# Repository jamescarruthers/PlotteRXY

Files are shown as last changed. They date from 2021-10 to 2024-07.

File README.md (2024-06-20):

# PlotteRXY
A machine designed to be your second plotter after an AxiDraw or vintage plotter.

# Why?
I really enjoyed the flexibility of my AxiDraw, and the speed of my Roland DPX-2200. I wanted something of a halfway house, with the pen flexibility of the AxiDraw and the speed and size of the Roland.

I set myself a few design requirements; enclosed inside a frame, scalable to any size including "massive" and a solenoid for fast pen lift.

I chose CoreXY pretty much just because I thought it was cool. It probably limits the scalability a bit as I expect belt droop might be an issue for _really_ huge plotters.

It uses an off-the-shelf FYSETC E4 controller board, which also has the benefit of being wifi enabled and has a web GUI built in.

The toolchain is fairly simple; SVG ingested in to VPYPE and it's G-code plugin. The G-code is uploaded through the web browser.

# How?

The build is fairly simple, you'll need access to a 3D printer to print off the various parts. Most of the parts are symetrical, so it's a fairly simple list of parts.

Ideally, print the parts in at least PETG but ASA or ABS would probably be better. My prototype machine has had no issues with matte PLA, which is probably the most brittle filament there is.

Suggested print settings; 4 walls, 5 top and bottom layers, 40% cubic infill.

Print time on a Bambu P1S is approx 13 hours at normal speed, and can be done over two plates. It uses 350g of filament in total.

The rest of the parts you'll need are here; https://docs.google.com/spreadsheets/d/1bjWigQsAcE3DGmHS4qicfL3H79G1RvEPnRx3VYNnScU/

There is a build guide in the hardware folder.

The firmware folder contains the machine configuration for use with FluidNC.

The software folder contains a configuration file for use with vpype and vpype-gcode.

# Donate

If you appreciate this project, please consider donating; https://www.paypal.com/donate/?hosted_button_id=BHS97LUK2LCB6

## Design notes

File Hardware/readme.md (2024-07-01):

*The 2040 Y-axis is depreciated at this time.* Only print one Y-axis folder - depending on what extrusion profile you are using for your y-axis. Unless you are making a giant A0 or larger plotter then use the 2020 sized version. Note that this design hasn't been tested above A1 size.

# How long should my extrusions be?

Let's say you want to build an A2 machine; 600 x 420 (rounded up)

X extrusion = width + 260 = 600 + 260 = 860mm

Y extrusion = length + 200 = 420 + 200 = 620mm

Y axis = Y extrusion - 13 = 607mm

These numbers have a bit of excess to allow a bit of movement around the outside of the plot area.

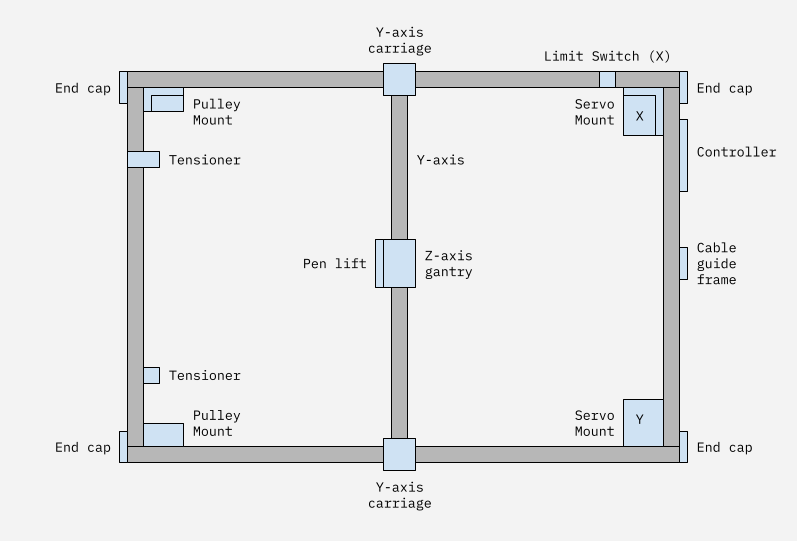
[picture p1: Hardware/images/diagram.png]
Naming diagram


# Hardware build guide

1. Print out a corner pulley mount and check that it fits snuggly into your v-slot extrusion. If it doesn't you might need to recalibrate your printer.
2. Print out all the parts. The number at the end of the filename is the quantity you'll need — so Pulley_2.3mf means you need 2.
3. Layout out the extrusion and printed parts on a table according to the diagram above, work out where you will need to insert t-nuts. This is important because once you start assembly certain t-nuts are impossible to insert without loosening and/or disassembling.
4. Build up the z-axis gantry and slide it on to the y-axis. The wheels should have shims and spacers on either side.
5. Build up the y-axis carriages and attach them to the y-axis extrusion. All pulleys sit on a single shim and have two shims between the F605 bearings. Keep the screws that hold it to the y-axis loose for now.
6. Install the end caps and servo mounts to the extusions so you have an open sided C shape. Note the orientation of the servo mounts, they are opposite ways up with the flat part in the middle of the extrusion.
7. Slide the whole y-axis assembly on to the extrusion.
8. Install the pulley mounts, end caps and attach the final extrusion to close the frame.
9. Adjust all the mount screws until the frame is square. Adjust the eccentric nuts. The y-axis should slide left to right freely. Tighten the screws that hold the y-axis in place.
10. Install all the pulleys. They pulleys should sit on a single shim spacer, with two shims in between the two bearings.
11. Install the servos in to the servo mounts, being sure to vertically align the toothed pulley with the pulleys on the mount. Depending on the pulley you may need to use one of the stepper spacers between the motor and the mount to align the belt so that it sits in the middle of the teeth on the pulley.
12. Install belts and attach to the belt tension plate. They should not be tight at this stage — but should not droop. Leave at least 80mm of extra belt so that you can adjust it later.

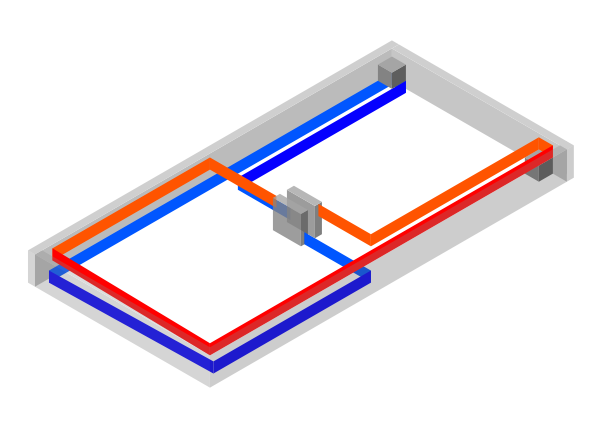
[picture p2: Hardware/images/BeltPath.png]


13. Use the tensioners to get the belt tight. It should not be super tight, but the belt should not droop.
14. Attach the belt tension plate to the z-axis gantry.
15. Move the y-axis towards and up against the corner pulley mounts. Check that the y-axis is square by ensuring the gap between the rounded part of the y-axis carriages have equal space against the corner pulley mounts. Each y-axis carriage should sit flat against the corner pulleys. If they're not, then this means each belt has uneven tension. Use the belt tensioners to adjust, they should only need minimal movement.
16. Build up pen lift and install on to gantry.

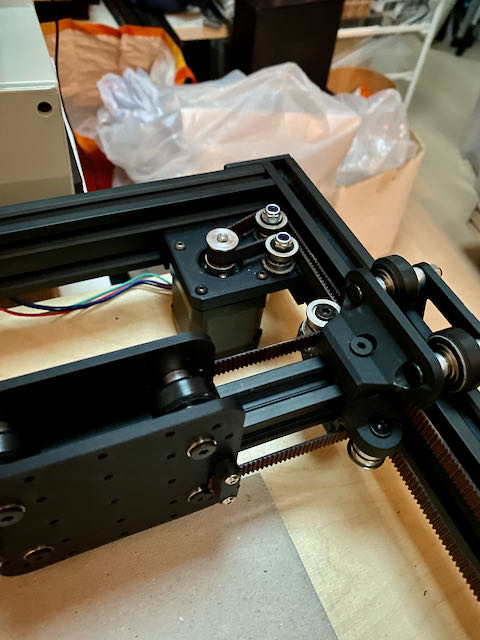
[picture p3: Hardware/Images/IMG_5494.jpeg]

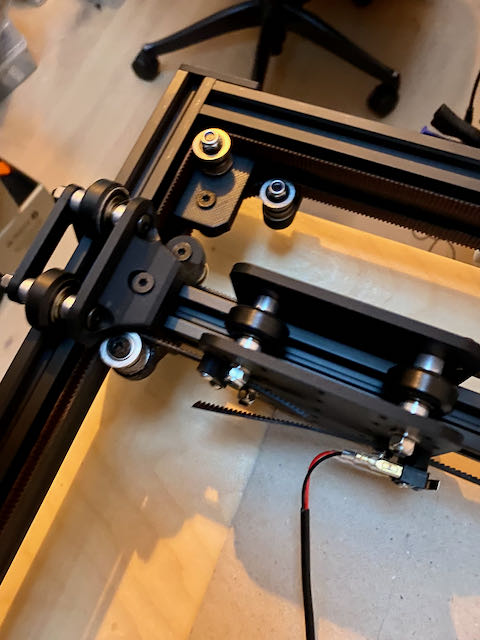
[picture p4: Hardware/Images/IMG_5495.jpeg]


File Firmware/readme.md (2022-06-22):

PlotterXY uses FluidNC: https://github.com/bdring/FluidNC

1. Install FluidNC on your FYSETC E4.
2. Upload the yaml config file to your board.
3. Restart the machine.

Be sure to use the supplied heatsinks, they should go on the rear of the board. I recommend using up the two spare heatsinks on the front of the ICs too.

*Note that the Y stepper is connected to the connector labelled Z-MOT – this is just to help thermals.

Connections:
* X-MOT: X stepper motor
* Z-MOT: Y stepper motor
* X-MIN: X limit switch
* Y-MIN: Y limit switch (on the z-axis gantry)
* HEATER: Solenoid

Check that these two jumpers are set for UART:

Jumpers

Before switching on the first time, move the gantry in to the centre of the work area. Turn on and connect to the web UI. Click on the clear alarm button. Use the jog function to check that the gantry moves in the correct direction. If it does not, then adjust the direction_pin in the config file from high to low on the relevant axis.

You will need to adjust the max_travel_mm and mpos_mm values in the config file for both the x and y axes to reflect the size of your plotter. The mpos_mm value should match the max_travel_mm. It is best to home the machine with the default settings, and then use a tape measure to get the dimensions. When homing move the z-gantry somewhere close to the top right by hand before you turn the plotter on, a couple of centimetres away from the limit swiches. Start off configuring it with a smaller size and then check out the movement of the machine with the jog function to make sure that the z-axis doesn't crash in to the right and bottom extrusions when you move it to 0,0.

Depending on your pen lift mechanism and pen weight you may need to adjust the solenoid pull_percent and hold_percent if the solenoid does not manage to lift or hold the pen.

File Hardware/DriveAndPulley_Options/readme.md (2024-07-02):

There are a few different options for drive and pulley configurations depending on what you want to achieve.

V2 is suggested for new builds as it's a much neater layout, allowing one end of the plotter to be free of belt and any kind of wiring. It also drives the middle of the belt, rather than more towards one end.

Note that there is no "upgrade path" from V2 to 4WD. If you want 4WD use the V1 mounts. There's nothing wrong with V1, it just drove the "wrong" part of the belt - which happens to be the right part for 4WD. If you _really_ want to go 4WD with V2 then you could use the V1 stepper mounts, but it's not optimal.

## V1 Original

* 2 x V1 stepper mount
* 2 x V1 pulley mount

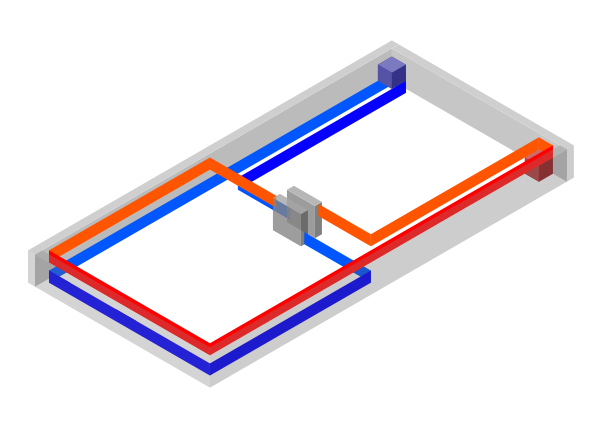
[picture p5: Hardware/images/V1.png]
V1


## V1 with 4-wheel-drive

* 2 x V1 stepper mount
* 2 x V1 stepper mount AWD

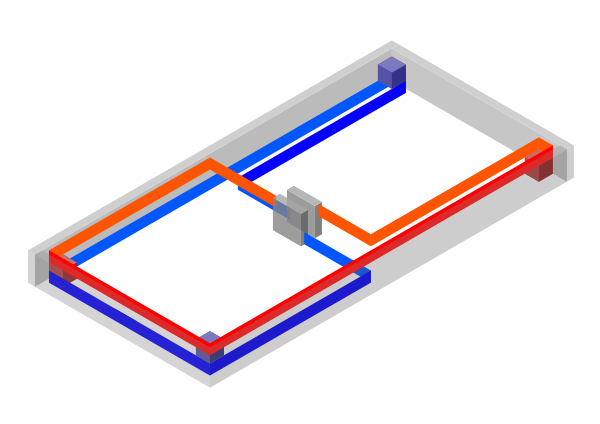
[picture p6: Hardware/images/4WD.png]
V1AWD


## > Note: V2 is currently untested - use at your own risk

## V2

* 2 x V2 stepper mount
* 2 x V2 pulley mount

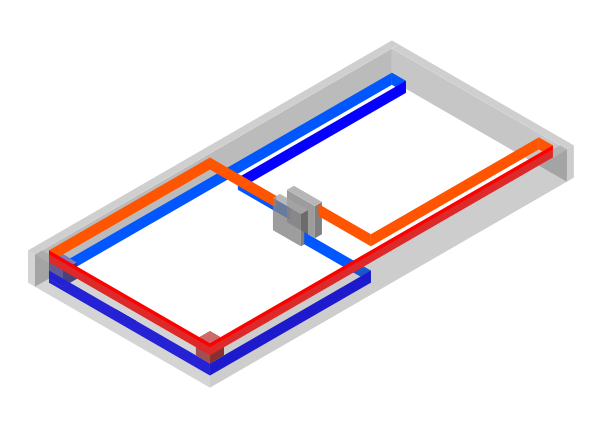
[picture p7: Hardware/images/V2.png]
V2


## V2 with central drive

* 1 x central drive
* 2 x V1 pulley mount
* 2 x V2 pulley mount

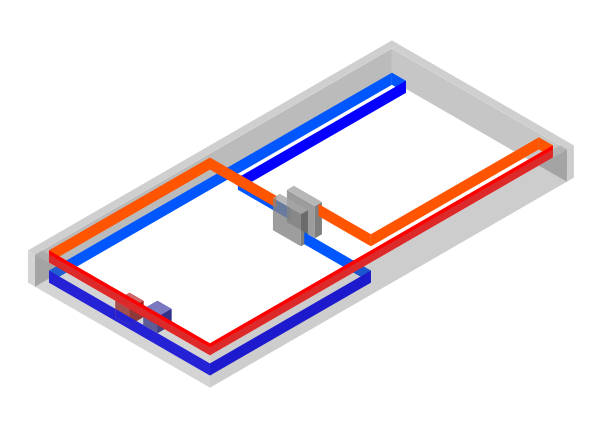
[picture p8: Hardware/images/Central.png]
V2 central drive


This configuration mounts the two steppers together.

## 4-wheel-drive tensioning procedure

Use the following procedure to make sure the pulley teeth are synchronised.

1. Power off the plotter.
2. Disconnect the two 4WD steppers from the controller board and loosen the two grub screws on both the 4WD pulleys.
3. Adjust the tension on both belts.
4. Power the plotter on.
5. Ensure the 4WD pulleys are engaged with the belt.
6. Tighten the grub screws on the 4WD pulleys, ensuring that they are not tightened against the flat of the D shaft. The pulley should not move as you tighten the grub screws.
7. Power the plotter off.
8. Reconnect the 4WD steppers.
9. Power the plotter on.

## Thoughts on drive position

Our aim is to drive a belt somewhere in the middle so that we have equal lengths on either side. A long belt is going to be more prone to vibration.

Below is a diagram showing the middle of the belt at different extents.

The red line shows the range and the red arrow shows the middle of the range. This is the ideal position for the driven pulley. We are constrained by putting the motor in a corner - luckily, a corner is not far away.

For 4-wheel-drive we would want to position motors at either end of the range.

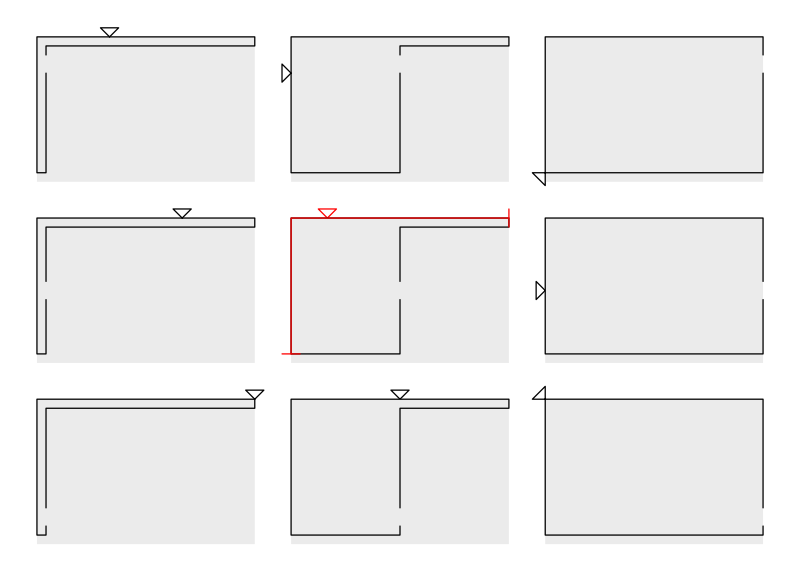
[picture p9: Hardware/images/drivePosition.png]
V2 central drive


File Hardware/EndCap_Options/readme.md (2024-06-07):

## End Cap Options

For a standard build you want to use the 4 x plain end caps.

For a 4WD build where you have motors at either end then choose either hole or XH. Depending on how you want to route your wires, you might want to use a mix of the plain and the end cap with XH or holes.

The XH variant has a slot that you can push an XH connector through - the most common type of connector on a stepper motor.

The hole variant is just a plain 4mm hole that you can put cables through.

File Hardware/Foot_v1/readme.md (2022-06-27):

These are some basic feet to get started with.

The lower part should be a tight enough fit with the foot so that it does not move.

The lower part needs to be secured to your worksurface with double sided tape.

An alternative would be to attach some rubber sheet to the lower part with double sided tape.

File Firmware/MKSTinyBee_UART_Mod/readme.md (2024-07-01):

To modify the MKS TinyBee to work with UART you'll need to jump various points on the board.

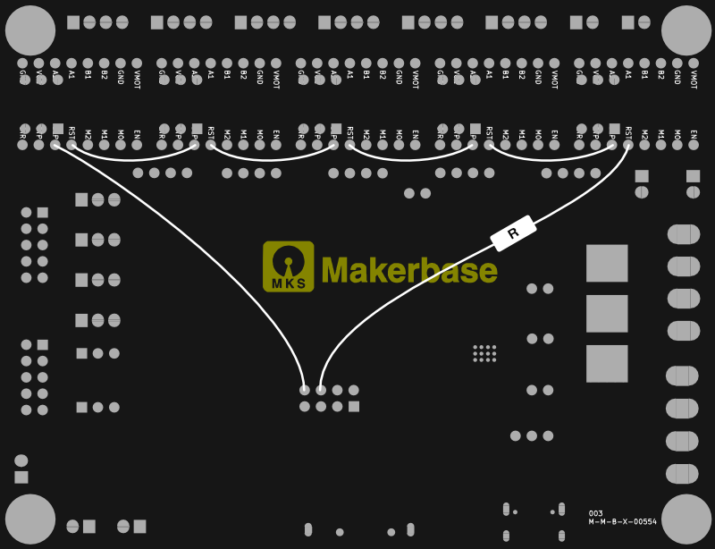
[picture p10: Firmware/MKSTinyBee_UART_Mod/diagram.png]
Diagram of modification


The resistor I used was 330R - you may need to try higher or lower.

Before installing the drivers switch all the dip switches to low.

Set the address of the X, Y and Z:

X = off off off
Y = on off off
Z = off on off

E0 is the secondary X - so set this to the same as X.
E1 is the secondary Y - so set this to the same as Y.

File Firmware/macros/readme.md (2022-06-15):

A series of macros useful for operating the plotter.
The park macro will need to be updated to reflect the size of your machine.

zero = move to 0,0

park = move the gantry out of the way to the top right

The A*_UR macros are for helping to align materials. Run the home macro, then place the bottom left corner of your material where the pen is – then run the A*_UR macro and align the top right corner.

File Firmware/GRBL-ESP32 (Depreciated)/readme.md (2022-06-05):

PlotterXY uses Grbl_ESP32: https://github.com/bdring/Grbl_Esp32

1. Download Grbl_ESP32. Follow the instructions.
2. Copy the PlotterXY_E4.h file to the machines folder and adjust the config.h to point towards it. See the section "Customize "Grbl_Esp32/src/Machine.h"" in the installation part of the wiki.
3. Compile and upload to the FYSETC E4 board. (remember that the board needs power!)

Connections:
* X-MOT: X stepper motor
* Y-MOT: Y stepper motor
* X-MIN: X limit switch
* Y-MIN: Y limit switch (on the z-axis gantry)
* HEATER: Solenoid

You will also need to use two jumpers to enable TMC2209 UART:

Jumpers

You will need to adjust the DEFAULT_X_MAX_TRAVEL and DEFAULT_Y_MAX_TRAVEL to reflect the size of your plotter. It's safer to do this after the firmware is compiled and uploaded, and you can use the jog function to move the gantry in to the 0,0 position.

Before switching on the first time, move the gantry in to the centre of the work area. Turn on and connect to the web UI. Click on the clear alarm button. Use the jog function to check that the gantry moves in the right direction. If it doesn't, then adjust the stepper motor direction in config.

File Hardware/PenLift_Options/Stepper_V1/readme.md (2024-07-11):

# Stepper pen lift

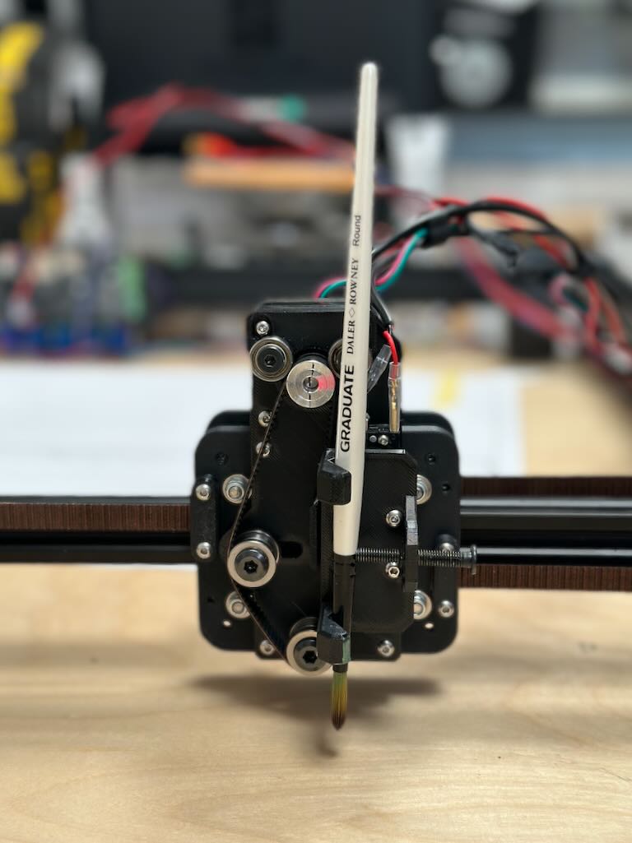
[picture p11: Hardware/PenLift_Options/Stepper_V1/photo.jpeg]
Stepper pen lift


This pen lift allows gravity and driven functions by adjusting a pulley.

Additional components required:

* Nema 17 stepper motor - pick the slimmest and lightest you can find
* 20t pulley - same used on the belt drive steppers
* 4 x 605Z bearings - same as used on all other pulleys
* 9mm 2GT belt - same as used for the drive belts
* 2 x 3mm spacers or 6 x 1mm spacers - same as used on all other pulleys
* 2 x 16mm M5 for pulleys
* 1 x 5mm t-nut - same as used for securing everything else to aluminium rail
* 1 x LWL7B 55mm guide rail - same as the solenoid lift
* 1 x limit switch and associated wiring - same as used on the limit switches for the X and Y axis
* 1 x M5 bolt for pen holder
* 2 x 605 bearings for the pulley keeper - this is the same as the rest of the plotter BUT without the flange
* Various M2 and M3 screws to mount the arm, penholder, limit switch and stepper motor

The pulley keeper should not be tight, it should just sit on the belt.

The belt should be installed with the adjustment pulley to the left, move the pulley to the right to loosen and enable "drop" mode.

The screw tip is a very basic item to put on the end of the pen holder bolt - it's a clumsy solution at the moment.

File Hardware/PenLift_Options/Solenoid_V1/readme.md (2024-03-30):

You will also need a suitable size e-clip, as well as a very short piece of silicon tubing to create a bumper.

The bumper should be just long enough to stop the solenoid from clacking.

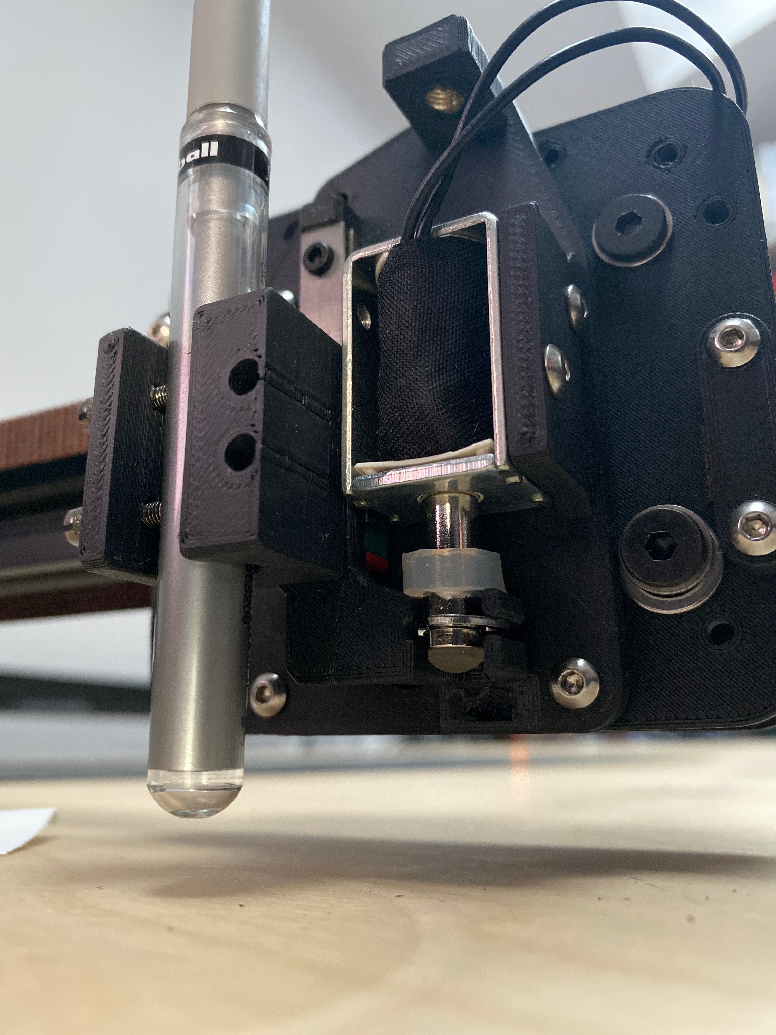
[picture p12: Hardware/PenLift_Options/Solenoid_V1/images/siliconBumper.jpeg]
Naming diagram


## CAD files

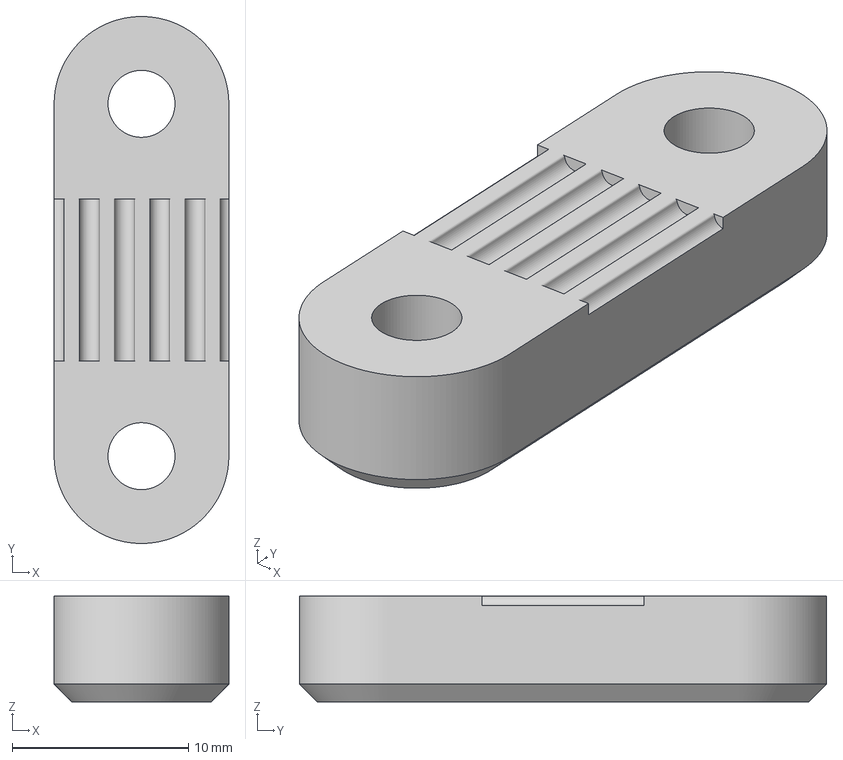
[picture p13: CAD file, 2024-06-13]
Hardware/BeltClamp_3.3mf
9.92 x 29.9 x 6.00 mm

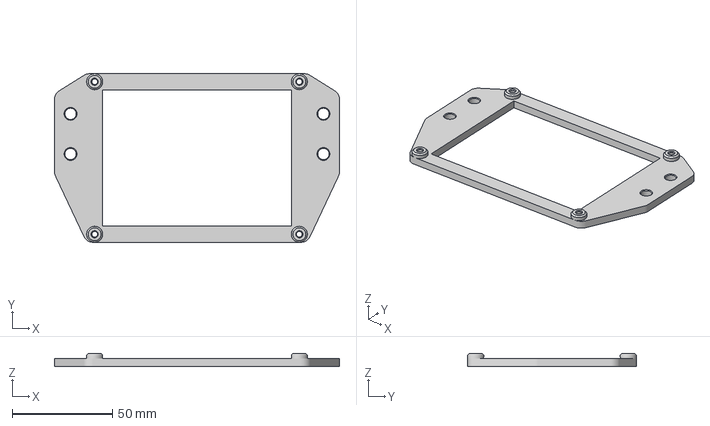
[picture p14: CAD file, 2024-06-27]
Hardware/BoardMount_Options/MKSTinyBee_Mount.3mf
142.0 x 84.0 x 6.60 mm

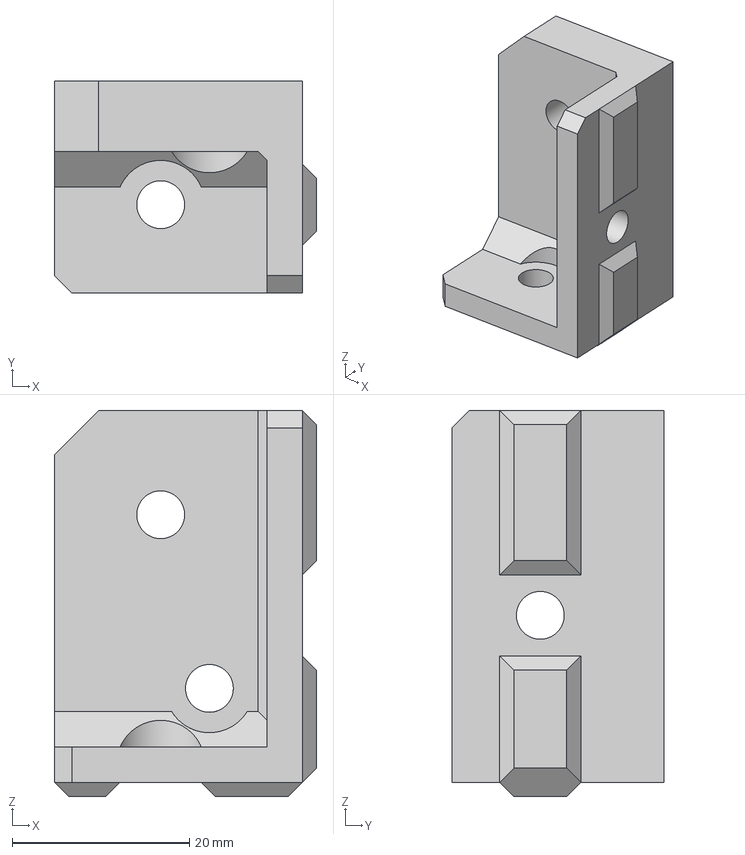
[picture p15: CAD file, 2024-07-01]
Hardware/DriveAndPulley_Options/V2_PulleyMount_2.3mf
29.6 x 24.0 x 43.6 mm

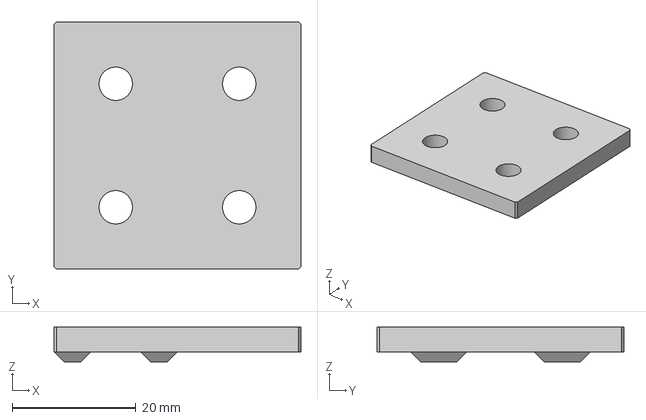
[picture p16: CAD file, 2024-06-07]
Hardware/EndCap_Options/EndCap.3mf
40.0 x 40.0 x 5.60 mm

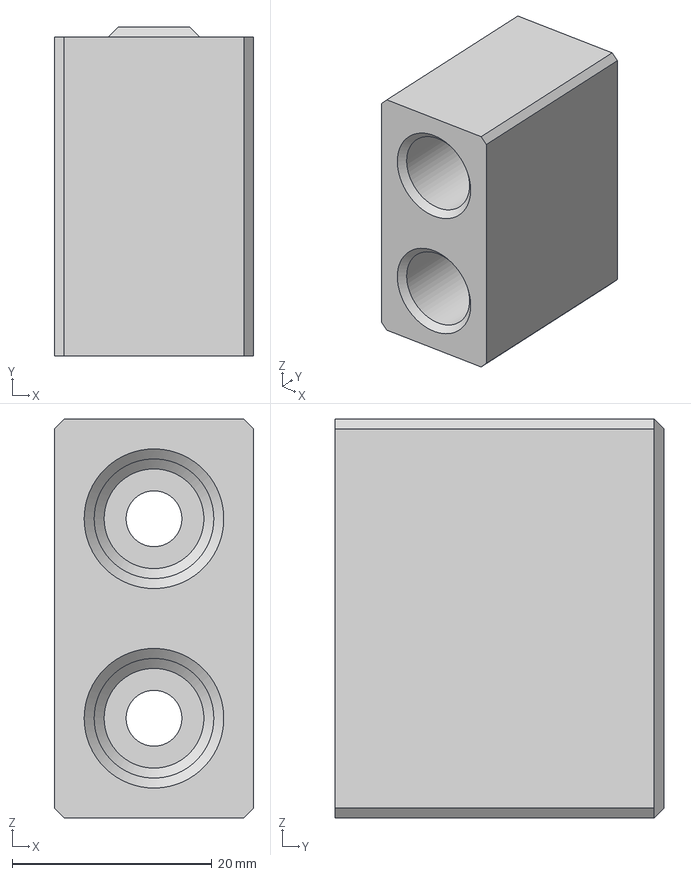
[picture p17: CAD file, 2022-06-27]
Hardware/Foot_v1/Foot_4.3mf
20.0 x 33.0 x 40.0 mm

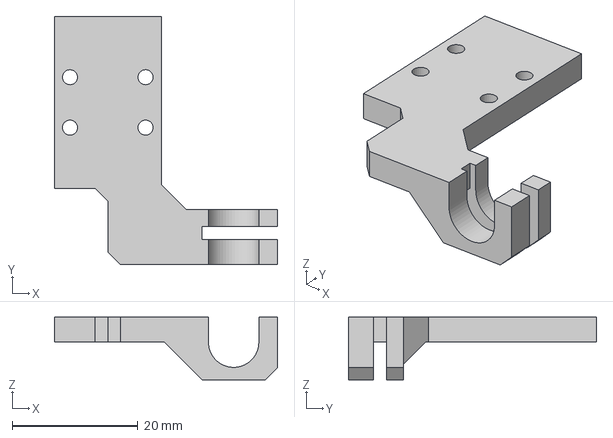
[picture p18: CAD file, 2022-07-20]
Hardware/PenLift_Options/Solenoid_V1/Lever.3mf
35.5 x 39.4 x 10.0 mm

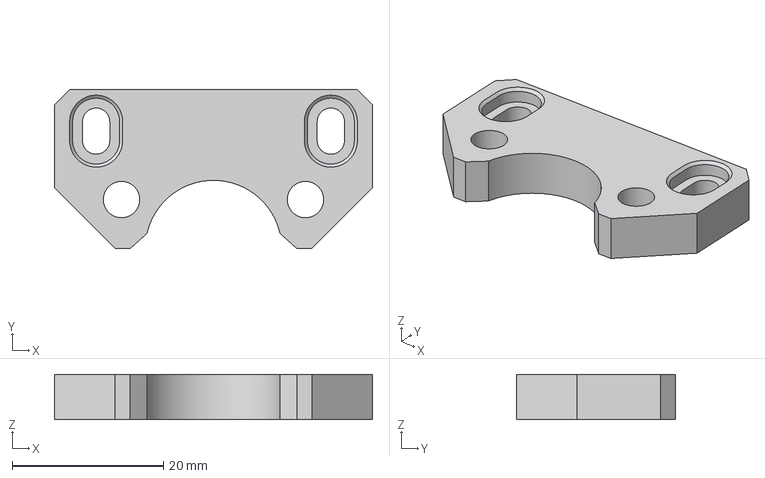
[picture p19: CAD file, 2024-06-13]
Hardware/PenLift_Options/Stepper_V1/pulleykeeper_1.3mf
42.0 x 21.0 x 6.00 mm

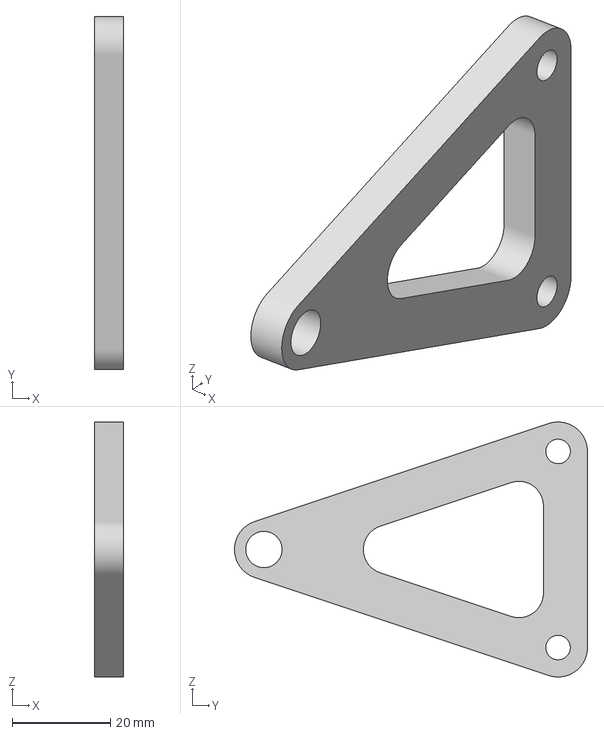
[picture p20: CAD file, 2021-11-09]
Hardware/Y-axis_Options/Y-axis_2020/YAxisCarriageSupport_2.3mf
6.00 x 72.0 x 52.0 mm

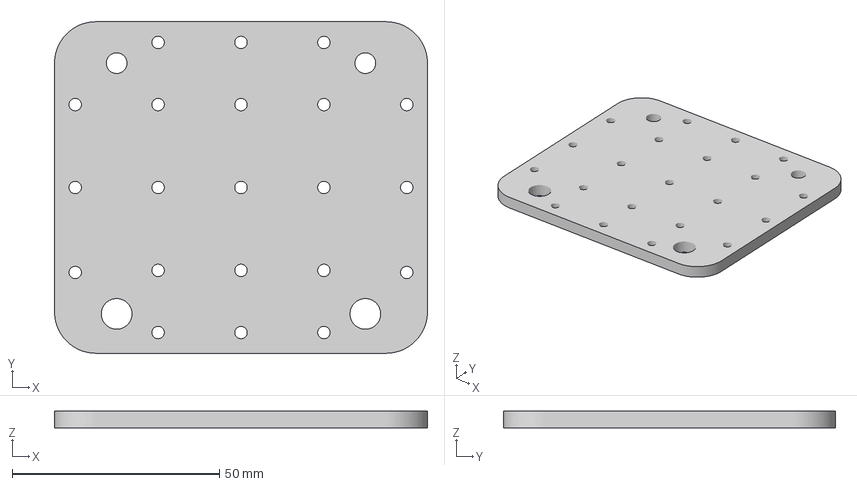
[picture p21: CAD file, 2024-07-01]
Hardware/Y-axis_Options/Y-axis_2040/ZAxisGantry2040_2.3mf
90.0 x 80.0 x 4.00 mm

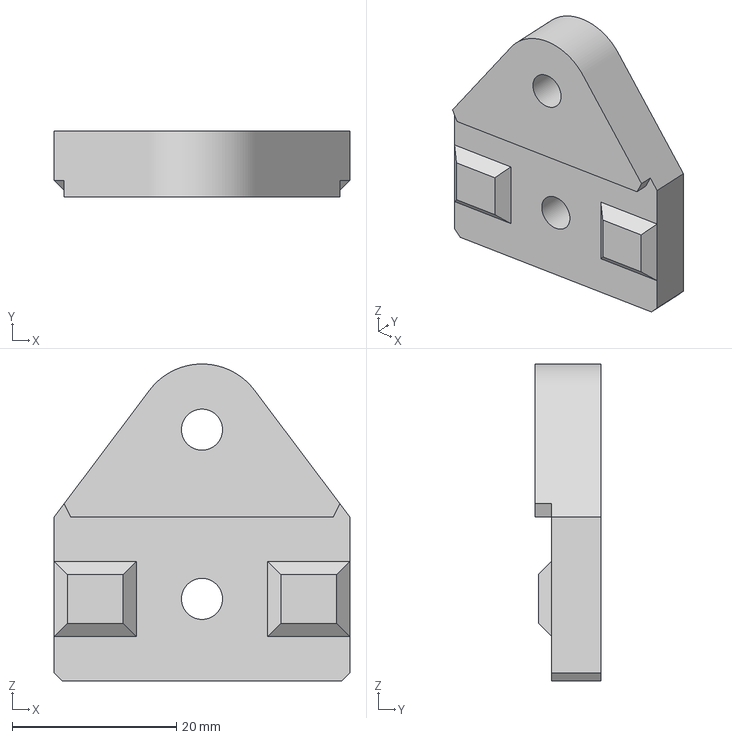
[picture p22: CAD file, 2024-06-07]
Hardware/BeltTensioner_2.3mf
36.0 x 8.00 x 38.6 mm

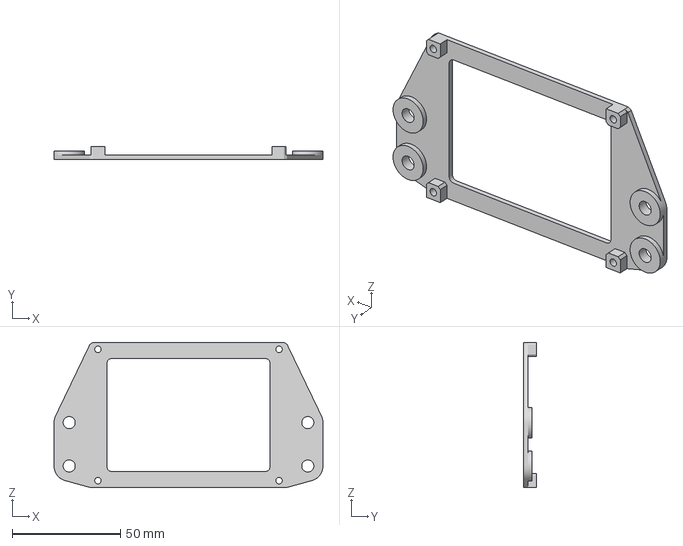
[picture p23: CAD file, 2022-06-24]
Hardware/BoardMount_Options/FYSETC_E4_Mount.3mf
124.0 x 6.00 x 67.0 mm

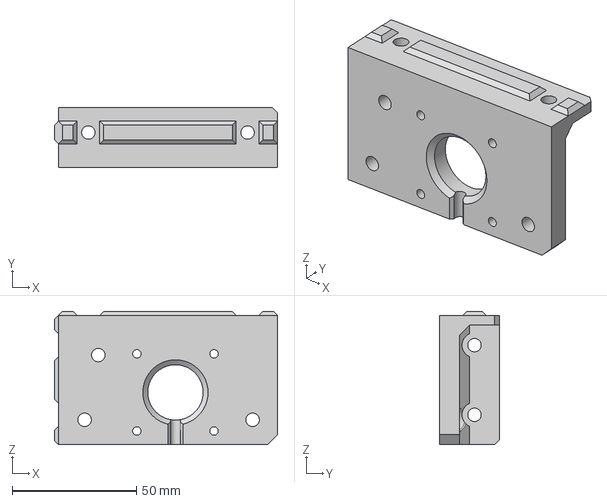
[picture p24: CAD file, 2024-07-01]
Hardware/DriveAndPulley_Options/V2_StepperMount_2.3mf
89.6 x 24.0 x 53.6 mm

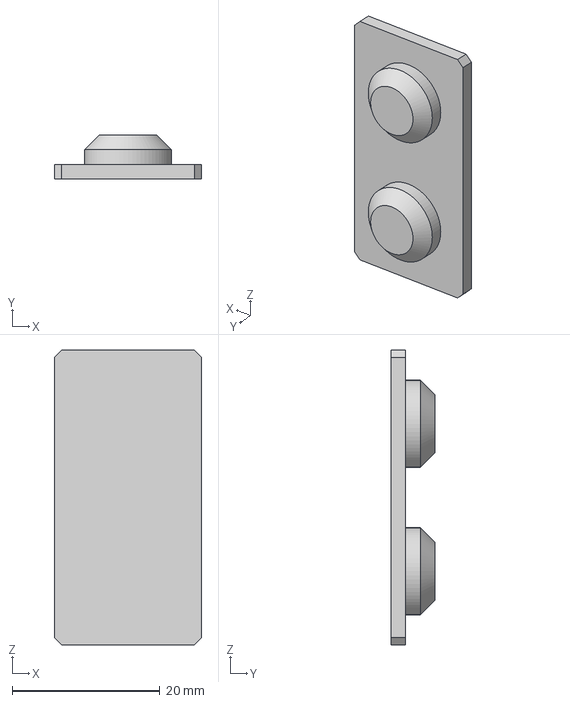
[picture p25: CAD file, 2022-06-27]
Hardware/Foot_v1/FootLower_4.3mf
20.0 x 6.00 x 40.0 mm

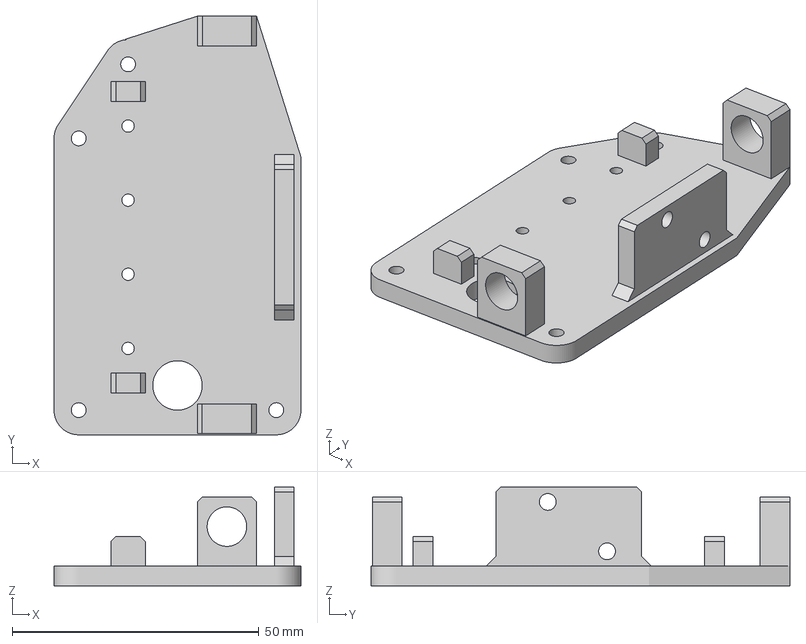
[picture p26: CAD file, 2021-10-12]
Hardware/PenLift_Options/Solenoid_V1/Mount.3mf
50.0 x 84.8 x 20.0 mm

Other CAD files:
Hardware/EndCap_Options/EndCap_Hole.3mf
Hardware/PenLift_Options/Stepper_V1/penholder_1.3mf
Hardware/Y-axis_Options/Y-axis_2020/ZAxisGantry_2.3mf
Hardware/Y-axis_Options/Y-axis_2040/YAxisCarriageSupport_2.3mf
Hardware/BeltClampLimit_1.3mf
Hardware/BeltTensionPlate_1.3mf
Hardware/CableClip_6.stl
Hardware/CableGuide_Frame.3mf
Hardware/CableGuide_Gantry.3mf
Hardware/DriveAndPulley_Options/CentralDrive_1.3mf
Hardware/DriveAndPulley_Options/StepperSpacer_2.3mf
Hardware/DriveAndPulley_Options/V1_PulleyMount_2.3mf
Hardware/DriveAndPulley_Options/V1_PulleyMount_Cover_A_1.3mf
Hardware/DriveAndPulley_Options/V1_PulleyMount_Cover_B_1.3mf
Hardware/DriveAndPulley_Options/V1_StepperMount_2.3mf
Hardware/DriveAndPulley_Options/V1_StepperMount_4WD_2.3mf
Hardware/DriveAndPulley_Options/V1_StepperMount_Cover_A_1.3mf
Hardware/DriveAndPulley_Options/V1_StepperMount_Cover_B_1.3mf
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

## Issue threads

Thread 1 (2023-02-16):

STEP Files Available?

ScottEgan, 2023-02-16:
Hi,

Awesome project, thanks for all the detail!

I'm in the process of modifying my plotter to be corexy and would like to use some of your parts with slight modifications. Do you have the STEP files available?

Thank you!

jamescarruthers, 2023-02-23:
Hi,

The project is designed in Fusion 360 — so I don't think STEP is available.

James

ScottEgan, 2023-02-23:
Hi James,

Thank you for the reply. Is it possible to export the native Fusion files then? I should be able to handle converting them.

TacyPW, 2024-03-15:
it would be really nice to have the fusion files in the repo as well

lambda1103, 2024-06-17:
Just to second (or third :D) this, I'd also appreciate it if you could share the .f3d file. Would be very helpful for assembly and small modifications.

theredwonder, 2024-09-03:
Wanted to also add an upvote for native CAD files. A ZIP of the Fusion360 assembly would be huge! All of the parts in STEP format would also be super helpful.
https://www.reddit.com/r/Fusion360/comments/1691l3g/export_formats_fusion_360_personalfree/

Looking to start a build on this soon, but am starting with a slightly different aluminum extrusion. Would love to tweak to fit. Thanks!

mattkerrison, 2025-03-03:
@jamescarruthers any chance of an update here? Either the f3d file or step files? I have a heap of Vslot left over from a cnc build but a lot of it isn’t 2020 or 2040 so it’d be good to adapt the 3d printed parts

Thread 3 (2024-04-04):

BOM Eccentric spacer count

TacyPW, 2024-04-04:
The BOM only lists 4 Ecc. Spacers for the Y axis gantries but as far as i can tell 4 more are needed for the Z gantry as well.

jamescarruthers, 2024-04-04:
Good catch! Thank you! Have updated the BOM.

Closed 2024-04-04.

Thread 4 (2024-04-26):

FluidNC Config File not compatible with latest version of fluidnc

TacyPW, 2024-04-26:
The way that fluidnc wants uart channels to be set up has changed, see [this page](http://wiki.fluidnc.com/en/config/uart_sections) of the wiki.

> Trinamic UART devices like TMC2208 and TMC2209 no longer support the subordinate "uart:" subsection (making that work was just too hard); you must use the external UART section with "uart_num: N":

the solution is to put the uart definition at the top level of the config file and then refer to it in each motor config.

this is uart section:
```yaml
uart2:
  txd_pin: gpio.22
  rxd_pin: gpio.21
  baud: 115200
  mode: 8N1
```
and this is one of the motor configs:
```yaml
 motor0:
      limit_pos_pin: gpio.34:high
      hard_limits: true
      pulloff_mm: 10.000
      tmc_2209:
        uart_num: 2
        addr: 1
        r_sense_ohms: 0.110
        run_amps: 1.200
        hold_amps: 0.800
        microsteps: 4
        stallguard: 0
        stallguard_debug: false
        toff_disable: 0
        toff_stealthchop: 5
        toff_coolstep: 3
        run_mode: StealthChop
        homing_mode: StealthChop
        use_enable: true
        step_pin: gpio.27
        direction_pin: gpio.26:high
        disable_pin: NO_PIN
```
i have this up and running on my machine and it seems to work just fine.

TacyPW, 2024-04-26:
for reference here is my whole config file:
```yaml
name: "PlotterXY"
board: "FYSETC E4"

stepping:
  engine: RMT
  idle_ms: 255
  dir_delay_us: 2
  pulse_us: 2
  disable_delay_us: 0
  segments: 20

kinematics:
  corexy:

uart2:
  txd_pin: gpio.22
  rxd_pin: gpio.21
  baud: 115200
  mode: 8N1

# 20t pulley
# steps per mm/microsteps   80/16   40/8    20/4    10/2    5/1
# resolution in mm          0.0125  0.025   0.050   0.100   0.200

# 16t pulley
# steps per mm/microsteps   100/16  50/8    25/4    12.5/2  6.25/1
# resolution in mm          0.010   0.020   0.050   0.080   0.160

# 1/4 microsteps gives best torque for a wide range of speeds

# Board stepper driver address and gpio
# axis  add   step  dir
# x     1     27    26
# y     3     33    32
# z     0     14    12
# e     2     16    17

axes:

  x:
    steps_per_mm: 20
    max_rate_mm_per_min: 24000
    acceleration_mm_per_sec2: 2400
    max_travel_mm: 431
    soft_limits: true
    homing:
      cycle: 2
      allow_single_axis: true
      mpos_mm: 431
      positive_direction: true
      seek_mm_per_min: 4000
      feed_mm_per_min: 600
      settle_ms: 200
      seek_scaler: 1.100
      feed_scaler: 1.100

    motor0:
      limit_pos_pin: gpio.34:high
      hard_limits: true
      pulloff_mm: 10.000
      tmc_2209:
        uart_num: 2
        addr: 1
        r_sense_ohms: 0.110
        run_amps: 1.200
        hold_amps: 0.800
        microsteps: 4
        stallguard: 0
        stallguard_debug: false
        toff_disable: 0
        toff_stealthchop: 5
        toff_coolstep: 3
        run_mode: StealthChop
        homing_mode: StealthChop
        use_enable: true
        step_pin: gpio.27
        direction_pin: gpio.26:high
        disable_pin: NO_PIN

  y:
    steps_per_mm: 20
    max_rate_mm_per_min: 24000
    acceleration_mm_per_sec2: 2400
    max_travel_mm: 279
    soft_limits: true
    homing:
      cycle: 1
      allow_single_axis: true
      mpos_mm: 279
      positive_direction: true
      seek_mm_per_min: 4000
      feed_mm_per_min: 600
      settle_ms: 200
      seek_scaler: 1.100
      feed_scaler: 1.100

    motor0:
      limit_pos_pin: gpio.35:high
      hard_limits: true
      pulloff_mm: 10.000
      tmc_2209:
        uart_num: 2
        addr: 0
        r_sense_ohms: 0.110
        run_amps: 1.200
        hold_amps: 0.800
        microsteps: 4
        stallguard: 0
        stallguard_debug: false
        toff_disable: 0
        toff_stealthchop: 5
        toff_coolstep: 3
        run_mode: StealthChop
        homing_mode: StealthChop
        use_enable: true
        step_pin: gpio.14
        direction_pin: gpio.12:high
        disable_pin: NO_PIN

  z:
    steps_per_mm: 80
    max_rate_mm_per_min: 64000
    acceleration_mm_per_sec2: 4800
    max_travel_mm: 5

    motor0:
      solenoid:
        output_pin: gpio.2
        pwm_hz: 30000
        off_percent: 0.000
        pull_percent: 100.000
        hold_percent: 40.000
        pull_ms: 50
        direction_invert: false

spi:
  miso_pin: gpio.19
  mosi_pin: gpio.23
  sck_pin: gpio.18

sdcard:
  cs_pin: gpio.5
  card_detect_pin: NO_PIN

# run a fan off the 24V/5V fan header – switch on and off with the WebUI mist button or by issuing an M8 command, turn off with M9
coolant:
  mist_pin: gpio.13
  delay: 0

macros:
  startup_line0:
  startup_line1:
  macro0:
  macro1:
  macro2:
  macro3:

start:
  must_home: true

```

jamescarruthers, 2024-05-05:
Thank you, Tacy

Wauter, 2025-06-06:
I wasn't able to get this going with the yaml file in the repository, the x axis still has the uart section.

now, I just managed to get is going using the x and z stepper motor sockets - its quite likely maybe my board is defective on the y axis. but the config also seems a little smelly for y - still i could not get it going on my board after trying to correct.

this information suggests the config file is not correct for Y, but I still wasnt able to get it going with these details.
http://wiki.fluidnc.com/en/hardware/3rd-party/fysetc_e4 -> the fluidnc documentation suggests the y uart address is 2, not 0
https://github.com/FYSETC/FYSETC-E4 -> the E4 documentation says that Y-Step	is gpio 33 and Y-DIR is 32

I also identified a couple of changes to the config format (fluidnc version 3.9.7):
mist pin has a different syntax now. can add home current to config

This is my working config using the x and z steppers: (working as in the steppers turn while homing during bench wire test, i turned down the amperage on the motors for now to avoid overheat)

I would make a pull request but probably better to figure out the y issue first, if someone else could try/confirm with their setup..

`name: "PlotterXY"
board: "FYSETC E4"

stepping:
  engine: RMT
  idle_ms: 255
  dir_delay_us: 2
  pulse_us: 2
  disable_delay_us: 0
  segments: 20

kinematics:
  corexy:

# 20t pulley
# steps per mm/microsteps   80/16   40/8    20/4    10/2    5/1
# resolution in mm          0.0125  0.025   0.050   0.100   0.200

# 16t pulley
# steps per mm/microsteps   100/16  50/8    25/4    12.5/2  6.25/1
# resolution in mm          0.010   0.020   0.050   0.080   0.160

# 1/4 microsteps gives best torque for a wide range of speeds

# Board stepper driver address and gpio
# axis  add   step  dir
# x     1     27    26
# y     3     33    32
# z     0     14    12
# e     2     16    17

axes:

  x:
    steps_per_mm: 20
    max_rate_mm_per_min: 24000
    acceleration_mm_per_sec2: 2400
    max_travel_mm: 860
    soft_limits: true
    homing:
      cycle: 2
      allow_single_axis: true
      mpos_mm: 860
      positive_direction: true
      seek_mm_per_min: 4000
      feed_mm_per_min: 600
      settle_ms: 200
      seek_scaler: 1.100
      feed_scaler: 1.100

    motor0:
      limit_pos_pin: gpio.34:high
      hard_limits: true
      pulloff_mm: 10.000
      tmc_2209:
        uart:
          txd_pin: gpio.22
          rxd_pin: gpio.21
          baud: 115200
          mode: 8N1
        addr: 1
        r_sense_ohms: 0.110
        run_amps: 1.200
        hold_amps: 0.800
        microsteps: 4
        stallguard: 0
        stallguard_debug: false
        toff_disable: 0
        toff_stealthchop: 5
        toff_coolstep: 3
        run_mode: StealthChop
        homing_mode: StealthChop
        use_enable: true
        step_pin: gpio.27
        direction_pin: gpio.26:high
        disable_pin: NO_PIN

  y:
    steps_per_mm: 20
    max_rate_mm_per_min: 24000
    acceleration_mm_per_sec2: 2400
    max_travel_mm: 600
    soft_limits: true
    homing:
      cycle: 1
      allow_single_axis: true
      mpos_mm: 600
      positive_direction: true
      seek_mm_per_min: 4000
      feed_mm_per_min: 600
      settle_ms: 200
      seek_scaler: 1.100
      feed_scaler: 1.100

    motor0:
      limit_pos_pin: gpio.35:high
      hard_limits: true
      pulloff_mm: 10.000
      tmc_2209:
        addr: 0
        r_sense_ohms: 0.110
        run_amps: 1.200
        hold_amps: 0.800
        microsteps: 4
        stallguard: 0
        stallguard_debug: false
        toff_disable: 0
        toff_stealthchop: 5
        toff_coolstep: 3
        run_mode: StealthChop
        homing_mode: StealthChop
        use_enable: true
        step_pin: gpio.14
        direction_pin: gpio.12:high
        disable_pin: NO_PIN

  z:
    steps_per_mm: 80
    max_rate_mm_per_min: 64000
    acceleration_mm_per_sec2: 4800
    max_travel_mm: 5

    motor0:
      solenoid:
        output_pin: gpio.2
        pwm_hz: 30000
        off_percent: 0.000
        pull_percent: 100.000
        hold_percent: 40.000
        pull_ms: 50
        direction_invert: false

spi:
  miso_pin: gpio.19
  mosi_pin: gpio.23
  sck_pin: gpio.18

sdcard:
  cs_pin: gpio.5
  card_detect_pin: NO_PIN

# run a fan off the 24V/5V fan header – switch on and off with the WebUI mist button or by issuing an M8 command, turn off with M9
coolant:
  mist_pin: gpio.13
  delay: 0

macros:
  startup_line0:
  startup_line1:
  macro0:
  macro1:
  macro2:
  macro3:

start:
  must_home: true
`

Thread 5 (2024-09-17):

Idea: fan output -> arduino nano -> servo to control pen

bushmango, 2024-09-17:
I'm working on prototyping some smaller plotters and am trying to get the fan output on the E4 board to talk to an arduino nano to use a simple servo to lift and drop a pen. Would this be a worthwhile alternative to the stepper or solenoid approach?

jamescarruthers, 2025-05-08:
You should be able to use the fan output directly - without the Nano.

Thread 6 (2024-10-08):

What length of bolts and how many?

bushmango, 2024-10-08:
From this segment of the bill of materials, I'm assuming these are the D5M4 bolts that you linked to on Aliexpress.

The quantity and length of the bolt aren't listed and I'm not sure what they are for.
Do you need one for each wheel?

I ordered the rest of the parts except for this and the 2.5mm bolt for linear guide which I also don't know the length of.

<<
5-M4 Shoulder bolts |   |   |   | 5mm shoulder, 4mm thread - I recommend these over normal bolts as I found some bolts are not straight - causing issues with wheels being misaligned | https://www.aliexpress.com/item/1005003510534996.html
>>

I'll happily put in a pull request with an updated bill of materials when I get mine assembled.

Thanks in advance! I'm excited for this project

jamescarruthers, 2025-05-08:
Sorry for the delay in reply - they're for the wheels.

I hope you got it sorted in the end.

kaosbeat, 2025-05-08:
I think they are supposed to go for example here

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

If I unbderstand the allieexpress link from the BOM correctly

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

1mm+4mm+6mm+12mm+6mm+4mm+1mm = 34mm

The only thing that really matters is L meaning for the wheels in the screenshot I would order the 35mm lengths and put some extra washers if needed.

Is this correct?

found some more minor errors in the BOM (this one https://github.com/jamescarruthers/PlotteRXY/issues/3 )
I can continue my work and keep track of the mistakes.. I'll report back.

jamescarruthers, 2025-05-08:
Yep! That's exactly it.

Just found them in my emails - I ordered 10 x 35mm and 5 x 30mm (it was 5 as that was the min quantity)

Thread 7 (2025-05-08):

would 2m by 1m  frame size be 'massive'?

kaosbeat, 2025-05-08:
As in... would that be too big for the belts to handle? would putting it upright mean less belt droop?
I have a roland DXY-1300, but I cannot find the right upgrade vintage plotter so I ended here.
Your project seems a fit, but I'm wondering about the max size...

jamescarruthers, 2025-05-08:
I've built one sized for A1, and I've seen bigger being built (Andee Collard) - you may run into limitations such as speed etc but it will work (is my summation)

kaosbeat, 2025-05-08:
Cool, I'm on it...

Closed 2025-05-08.

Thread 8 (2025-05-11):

solenoid voltage

kaosbeat, 2025-05-11:
I'm building the plotter with the solenoid option.
The solenoid from the BOM is 12V, I'm working with the [FYSETC-E4](https://github.com/FYSETC/FYSETC-E4) as suggested and 24V voltage as the main power source.
Where do I connect the solenoid? and is it safe to use the 12V solenoid on 24V?

Wauter, 2025-06-06:
Hey, not sure you still need it.

if you use the 12V solenoid with 24V, the current doubles from its intended rating. This can lead to overheating / melting in extreme case.

You are best getting a 24V rated solenoid, but for initial testing you can also:
 - just power the E4 with 12V, it will take it fine. Maybe your steppers will be less powerful, not too sure. (I am powering mine with 12 V to start with)
 - change the solenoid config setting to lower the duty cycle:
        off_percent: 0.000
                pull_percent: 100.000 -> change this to 100.000
                hold_percent: 40.000 -> change this to 20.000
        the effect of this is that by PWM, you will reduce the current by half, bringing it in line with the 12V spec.
however, if the controller for whatever reason gets stuck on 100% duty cycle you might have fire risk.. would not trust it except for testing.

kaosbeat, 2025-06-07:
Working with a lower duty cycle, for now no problem during prolonged use .
It does get burning hot, need to take care not to touch when swapping pens. For now doing supervised use only.
It works really well! Very happy with the build, but I'll look into swapping the solenoid

jamescarruthers, 2025-06-07:
In reality it doesn't really matter running at 24V.

You shouldn't need to run it at full power if it's setup right - the very short pull current is the biggest one, and then the hold should be a lot smaller.

Essentially - it runs cool.

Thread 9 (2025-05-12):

V wheels size required?

Wauter, 2025-05-12:
Hi,

I am currently looking into collecting the parts to build one of these.

one question:

the required size for the V wheels, the ali link is dead for me. I gather, from the bolts, that the ID is 5mm (4.9?), but I am not sure the size of the wheel, when browsing around,  I see 'small' 15.5 and 'big' 24.8 on offer ( https://www.aliexpress.com/item/1005004275676552.html )

do the wheels have to be a specific material? I assume hard plastic, like pom would be good?

---

some observations from a new set of eyes looking at the materials, just in case it is useful areas where things were maybe a bit unclear on first read.  (I think that is super fine BTW, and I appreciate  sharing the project in any form - just sharing in case this is useful to the project)

link for limit switches is dead - i assume plain old standard limit switches, which I have at hand

wasn't sure about the description of the v nuts, but I think I did figure it out. -> these plain old ones? https://www.aliexpress.com/item/32853205697.html

I struggled with the shoulder bolts, somehow - i am blind, since the required info is there now (I had missed the length), but I found the info in the related ticket on wiki. _(only now I opened the nuts and bolts section and behold it is all neatly there actually, whoops might be nice the have a little message in the first sheet about that for dummies like me..)_

would be great to have more angles on a finished printer for reference, but should be fine how it is as well.

kaosbeat, 2025-05-15:
Hey,

I put everything in 3D to check the sizes. About the bolts: https://github.com/jamescarruthers/PlotteRXY/issues/6#issuecomment-2863556965

I'm starting my built today, I'm expecting the parts later today so I will try and keep track of my progress

The wheels I bought are 24mm diameter, hopefully that is the right size

The limit switches, I'm still unsure what is the best approach, I have some from an old 3D printer. will test

Wauter, 2025-05-20:
great, good luck! I also ordered parts, only held off on the wheels for now and the solenoid.
first batch of parts arrived today, going to start printing this week.

jamescarruthers, 2025-05-20:
Good luck both of you!

The limit switches are just the typical standard size ones like this:

https://ooznest.co.uk/product/micro-limit-switch/

Wauter, 2025-05-21:
for anyone that needs to read this: regular 2020 profile is not the same as V-slot 2020 profile.. whoops

Closed 2025-06-06.

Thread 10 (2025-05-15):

4WD config file for FLuidNC

kaosbeat, 2025-05-15:
Documentetation in how to configure the 4WD option is scarce

taking this file https://github.com/jamescarruthers/PlotteRXY/blob/main/Firmware/FYSETCE4_plotterxy.yaml as a starting option, I think I need to add a` motor1:` section with the same layout as `motor0:` to both  x and y axes.

I'm using this table from https://github.com/FYSETC/FYSETC-E4

and I believe copying the motor0: section and changing

```
axes:
 x:
    motor1:
      step_pin: gpio.33
      direction_pin: gpio.32:high
 y:
    motor1:
      step_pin: gpio.16
      direction_pin: gpio.17:high

```

should already be a step in the good direction.
Anything important I need to change/add not listed here?

kaosbeat, 2025-05-20:
That was not enough.
I had to change the address of the stepper controllers as well.  So the sections
```

      tmc_2209:
        uart_num: 2
        addr: X
```

change X according to the table

# Board stepper driver address and gpio
# axis  add   step  dir
# x     1     27    26
# y     3     33    32
# z     0     14    12
# e     2     16    17

axes:
 x:
    motor1:
      tmc_2209:
        addr: 3
        step_pin: gpio.33
        direction_pin: gpio.32:high
 y:
    motor1:
      tmc_2209:
        addr: 2
        step_pin: gpio.16
        direction_pin: gpio.17:high

Closed 2025-05-20.

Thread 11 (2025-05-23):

4WD parts mounting schematic / belt

kaosbeat, 2025-05-23:
I'm struggling with how the belt fits the 4WD option. The normal side is exactly the same as the 2motor option, but how does the belt move at the opposite side?
I think I need to cross the belts like this?
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

and then?

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

and

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

This gives me a problem. The motor doesn't fit well and the bearings don't have enough free space because of the motor

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

Any help appreciated

kaosbeat, 2025-05-23:
apparently I printed one of the 4WD parts mirrored.. still dazzled though

is this how it should be?

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

jamescarruthers, 2025-05-23:
I'll take a photo - I need to add it to the repository anyway.

kaosbeat, 2025-05-26:
not yet operational, but taking shape

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

the 4WD is still unclear

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

I did it like this, but I cannot mount the corner screws because of the pully on the motor side.

I can off course modify the 3D and reprint, but it feels like I made a mistake ?

jamescarruthers, 2025-05-26:
Yep, you need to use flat head screws.

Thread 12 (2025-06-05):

Eccentric spacer required for gantry

Wauter, 2025-06-05:
Eccentric spacer (Type A - 6mm w/ 8mm AF): it appears the eccentric spacers are required to tighten up both gantry and carriage, but the hardware list only specifies 4 units.

did I get that wrong or are 8 eccentric spacers required?

jamescarruthers, 2025-06-05:
One on either carriage and then two on the toolhead carriage

Wauter, 2025-06-06:
okay this is a duplicate of this closed issue:
https://github.com/jamescarruthers/PlotteRXY/issues/3

eccentric spacer count in the BOM is still 4

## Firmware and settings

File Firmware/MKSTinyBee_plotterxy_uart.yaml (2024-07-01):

board: MKS TinyBee V1.0 XXYYZ
name: PlotterXY

kinematics:
  corexy:

i2so:
  bck_pin: gpio.25
  data_pin: gpio.27
  ws_pin: gpio.26

spi:
  miso_pin: gpio.19
  mosi_pin: gpio.23
  sck_pin: gpio.18

uart2:
  txd_pin: gpio.17
  rxd_pin: gpio.16
  baud: 115200
  mode: 8N1

sdcard:
  cs_pin: gpio.5
  # uses TH2 IO34 active low - MAKE SURE jumper J2 is set to SDDET!!!
  card_detect_pin: gpio.34:low

stepping:
  engine: I2S_STATIC
  idle_ms: 255
  pulse_us: 4
  dir_delay_us: 1
  disable_delay_us: 2

# 20t pulley
# steps per mm/microsteps   80/16   40/8    20/4    10/2    5/1
# resolution in mm          0.0125  0.025   0.050   0.100   0.200

# 16t pulley
# steps per mm/microsteps   100/16  50/8    25/4    12.5/2  6.25/1
# resolution in mm          0.010   0.020   0.050   0.080   0.160

# 1/4 microsteps gives best torque for a wide range of speeds


axes:
  x:
    steps_per_mm: 20
    max_rate_mm_per_min: 24000
    acceleration_mm_per_sec2: 2400
    max_travel_mm: 840
    soft_limits: true
    homing:
      cycle: 2
      positive_direction: true
      mpos_mm: 840
      feed_mm_per_min: 600
      seek_mm_per_min: 4000
      settle_ms: 500
      seek_scaler: 1.200
      feed_scaler: 1.200

    motor0:
      limit_pos_pin: gpio.33:high:pu
      hard_limits: true
      pulloff_mm: 4.000
      tmc_2209:
        uart_num: 2
        addr: 0
        r_sense_ohms: 0.110
        run_amps: 1.200
        hold_amps: 0.800
        microsteps: 4
        stallguard: 0
        stallguard_debug: false
        toff_disable: 0
        toff_stealthchop: 5
        toff_coolstep: 3
        run_mode: StealthChop
        homing_mode: StealthChop
        use_enable: true
        step_pin: I2SO.1
        direction_pin: I2SO.2
        disable_pin: I2SO.0

    # use E0 driver for 2nd X axis motor
    motor1:
      hard_limits: true
      pulloff_mm: 4.000
      tmc_2209:
        uart_num: 2
        addr: 0
        r_sense_ohms: 0.110
        run_amps: 1.200
        hold_amps: 0.800
        microsteps: 4
        stallguard: 0
        stallguard_debug: false
        toff_disable: 0
        toff_stealthchop: 5
        toff_coolstep: 3
        run_mode: StealthChop
        homing_mode: StealthChop
        use_enable: true
        step_pin: I2SO.10
        direction_pin: I2SO.11
        disable_pin: I2SO.9

  y:
    steps_per_mm: 20
    max_rate_mm_per_min: 24000
    acceleration_mm_per_sec2: 2400
    max_travel_mm: 590
    soft_limits: true
    homing:
      cycle: 1
      positive_direction: true
      mpos_mm: 590
      feed_mm_per_min: 600
      seek_mm_per_min: 4000
      settle_ms: 500
      seek_scaler: 1.200
      feed_scaler: 1.200

    motor0:
      limit_pos_pin: gpio.32:high:pu
      hard_limits: false
      pulloff_mm: 4.000
      tmc_2209:
        uart_num: 2
        addr: 1
        r_sense_ohms: 0.110
        run_amps: 1.200
        hold_amps: 0.800
        microsteps: 4
        stallguard: 0
        stallguard_debug: false
        toff_disable: 0
        toff_stealthchop: 5
        toff_coolstep: 3
        run_mode: StealthChop
        homing_mode: StealthChop
        use_enable: true
        step_pin: I2SO.4
        direction_pin: I2SO.5
        disable_pin: I2SO.3

    # use E1 driver for 2nd Y axis motor
    motor1:
      limit_neg_pin: NO_PIN
      hard_limits: false
      pulloff_mm: 4.000
      tmc_2209:
        uart_num: 2
        addr: 1
        r_sense_ohms: 0.110
        run_amps: 1.2
        hold_amps: 0.8
        microsteps: 4
        stallguard: 0
        stallguard_debug: false
        toff_disable: 0
        toff_stealthchop: 5
        toff_coolstep: 3
        run_mode: StealthChop
        homing_mode: StealthChop
        use_enable: true
        step_pin: I2SO.13
        direction_pin: I2SO.14
        disable_pin: I2SO.12

  z:
    # this is setup for a 0.9deg stepper motor - use 20 for 1.8deg
    steps_per_mm: 40
    max_rate_mm_per_min: 64000
    acceleration_mm_per_sec2: 6400
    max_travel_mm: 28
    soft_limits: true
    homing:
      cycle: 3
      positive_direction: true
      mpos_mm: 28
      feed_mm_per_min: 300.000
      seek_mm_per_min: 500.000
      settle_ms: 500
      seek_scaler: 1.200
      feed_scaler: 1.200

    motor0:
      limit_pos_pin: gpio.22:high:pu
      hard_limits: true
      pulloff_mm: 2.000
      # stepstick:
      #   step_pin: I2SO.7
      #   direction_pin: I2SO.8:low
      #   disable_pin: I2SO.6
      tmc_2209:
        uart_num: 2
        addr: 2
        r_sense_ohms: 0.110
        run_amps: 1.200
        hold_amps: 0.800
        microsteps: 4
        stallguard: 0
        stallguard_debug: false
        toff_disable: 0
        toff_stealthchop: 5
        toff_coolstep: 3
        run_mode: StealthChop
        homing_mode: StealthChop
        use_enable: true
        step_pin: I2SO.7
        direction_pin: I2SO.8:low
        disable_pin: I2SO.6



coolant:
  # Heated Bed Terminal Block
  flood_pin: i2so.16
  # HE0 Terminal Block
  mist_pin: i2so.17
  delay_ms: 0

start:
  must_home: true

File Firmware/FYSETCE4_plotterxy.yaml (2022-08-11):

name: "PlotterXY"
board: "FYSETC E4"

stepping:
  engine: RMT
  idle_ms: 255
  dir_delay_us: 2
  pulse_us: 2
  disable_delay_us: 0
  segments: 20

kinematics:
  corexy:

# 20t pulley
# steps per mm/microsteps   80/16   40/8    20/4    10/2    5/1
# resolution in mm          0.0125  0.025   0.050   0.100   0.200

# 16t pulley
# steps per mm/microsteps   100/16  50/8    25/4    12.5/2  6.25/1
# resolution in mm          0.010   0.020   0.050   0.080   0.160

# 1/4 microsteps gives best torque for a wide range of speeds

# Board stepper driver address and gpio
# axis  add   step  dir
# x     1     27    26
# y     3     33    32
# z     0     14    12
# e     2     16    17

axes:

  x:
    steps_per_mm: 20
    max_rate_mm_per_min: 24000
    acceleration_mm_per_sec2: 2400
    max_travel_mm: 860
    soft_limits: true
    homing:
      cycle: 2
      allow_single_axis: true
      mpos_mm: 860
      positive_direction: true
      seek_mm_per_min: 4000
      feed_mm_per_min: 600
      settle_ms: 200
      seek_scaler: 1.100
      feed_scaler: 1.100

    motor0:
      limit_pos_pin: gpio.34:high
      hard_limits: true
      pulloff_mm: 10.000
      tmc_2209:
        uart:
          txd_pin: gpio.22
          rxd_pin: gpio.21
          baud: 115200
          mode: 8N1
        addr: 1
        r_sense_ohms: 0.110
        run_amps: 1.200
        hold_amps: 0.800
        microsteps: 4
        stallguard: 0
        stallguard_debug: false
        toff_disable: 0
        toff_stealthchop: 5
        toff_coolstep: 3
        run_mode: StealthChop
        homing_mode: StealthChop
        use_enable: true
        step_pin: gpio.27
        direction_pin: gpio.26:high
        disable_pin: NO_PIN

  y:
    steps_per_mm: 20
    max_rate_mm_per_min: 24000
    acceleration_mm_per_sec2: 2400
    max_travel_mm: 600
    soft_limits: true
    homing:
      cycle: 1
      allow_single_axis: true
      mpos_mm: 600
      positive_direction: true
      seek_mm_per_min: 4000
      feed_mm_per_min: 600
      settle_ms: 200
      seek_scaler: 1.100
      feed_scaler: 1.100

    motor0:
      limit_pos_pin: gpio.35:high
      hard_limits: true
      pulloff_mm: 10.000
      tmc_2209:
        addr: 0
        r_sense_ohms: 0.110
        run_amps: 1.200
        hold_amps: 0.800
        microsteps: 4
        stallguard: 0
        stallguard_debug: false
        toff_disable: 0
        toff_stealthchop: 5
        toff_coolstep: 3
        run_mode: StealthChop
        homing_mode: StealthChop
        use_enable: true
        step_pin: gpio.14
        direction_pin: gpio.12:high
        disable_pin: NO_PIN

  z:
    steps_per_mm: 80
    max_rate_mm_per_min: 64000
    acceleration_mm_per_sec2: 4800
    max_travel_mm: 5
    
    motor0:
      solenoid:
        output_pin: gpio.2
        pwm_hz: 30000
        off_percent: 0.000
        pull_percent: 100.000
        hold_percent: 40.000
        pull_ms: 50
        direction_invert: false

spi:
  miso_pin: gpio.19
  mosi_pin: gpio.23
  sck_pin: gpio.18

sdcard:
  cs_pin: gpio.5
  card_detect_pin: NO_PIN

# run a fan off the 24V/5V fan header – switch on and off with the WebUI mist button or by issuing an M8 command, turn off with M9
coolant:
  mist_pin: gpio.13
  delay: 0

macros:
  startup_line0:
  startup_line1:
  macro0:
  macro1:
  macro2:
  macro3:

start:
  must_home: true

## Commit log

2021-10-12 Change filename
    [Lever_Top.3mf]
2021-10-13 Move 3MF to Hardware folder
    [BeltTensioner_2.3mf, CableGuide_Frame.3mf, CableGuide_Gantry.3mf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]
2021-10-14 Updated files
    [CableClip_6.stl, Gantry_2.3mf, Y-axis_carrier.3mf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]
2021-10-19 Update files
    [YAxisMountSupport_2.3mf]
2021-11-05 Changed files
    [PulleyMount_2.3mf, PulleyMount_2_Revised.3mf, ServoMount_2.3mf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]
2021-11-05 Updated mounts
    [PulleyMount_2_Revised.3mf, ServoMount_2_Revised.3mf]
2021-11-09 Updated filenames
    [YAxisCarriageSupport_2.3mf, YAxisCarriage_2.3mf, YAxisGantrySupport_2.3mf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]
2022-05-04 Added macros
    [home.g, park.g, penDown.g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]
2022-05-30 Updated macros to g00
    [home.g, park.g]
2022-05-30 Updated to G00 without F
    [home.g, park.g]
2022-06-01 Updated config.yaml
    [home.g, park.g]
2022-06-09 Updated config to include 16t and 20t pulley values
2022-06-11 Updated 2040 gantry
    [ZAxisGantry_2.3mf]
2022-06-12 Updated configs
    [BeltTensionPlate_1.3mf]
2022-06-15 Added some useful macros
    [A1_UR.g, A1park.g, A3_UR.g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]
2022-06-15 Updated macro
    [zero.g]
2022-06-16 Updated macros
    [A1_UR.g, disableMotors.g]
2022-06-27 Updated foot
    [Foot_Brace.3mf, Foot_Lower_4.3mf]
2022-06-27 Updated feet
    [Foot_4.3mf, Foot_Brace.3mf, Foot_Lower_4.3mf]
2022-07-20 More sensible max rates
    [Lever.3mf]
2022-07-21 Updated the gantry cable guide
    Updated the cable guide on the gantry to give slightly more height for the guide - it was drooping a bit too much on my A1 sized plotter
    [CableGuide_Gantry.3mf]
2022-07-22 Added stepper mount spacer
    [StepperMount_2.3mf, StepperSpacer_2.3mf]
2023-09-13 Update README.md with print settings
2024-05-05 Add files via upload
    Added pulley grub screw access slot
    [StepperMount_2.3mf]
2024-05-13 Updated mount and pulley options
    [CentralDrive_1.3mf, PulleyMount_2or4.3mf, StepperCornerMount_2.3mf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]
2024-05-13 Added belt path image
2024-05-14 Added drive and pulley options images
2024-05-14 Updated corner stepper
    [StepperCornerMount_2.3mf]
2024-05-18 Updateed endcaps
    [CentralDrive_1.3mf, EndCap.3mf, EndCap_Hole.3mf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]
2024-06-07 Added pulley mount covers and end caps
    [BeltTensioner_2.3mf, EndCap.3mf, EndCap_Hole.3mf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]
2024-06-13 General update and stepper pen lift added
    Updated belt clamp with grooves to provide better grip.
    Stepper pen lift V1
    [BeltClamp_3.3mf, Holder.3mf, Lever.3mf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]
2024-06-13 Added pulley keeper
    [pulleykeeper_1.3mf]
2024-06-13 Reorganised some files
    [YAxisCarriageSupport_2.3mf, YAxisCarriage_2.3mf, ZAxisGantry_2.3mf]
2024-06-27 Added TinyBee mount
    [FYSETC_E4_Mount.3mf, MKSTinyBee_Mount.3mf]
2024-07-01 Updated 2040 z gantry to match 2020
    [ZAxisGantry2040_2.3mf, ZAxisGantry_2.3mf]
2024-07-01 Updated naming
    [YAxisCarriage2040_2.3mf]
2024-07-01 Added EXPERIMENTAL V2 drive and pulley options
    [V1_PulleyMount_2.3mf, V1_PulleyMount_Cover_A_1.3mf, V1_PulleyMount_Cover_B_1.3mf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]
